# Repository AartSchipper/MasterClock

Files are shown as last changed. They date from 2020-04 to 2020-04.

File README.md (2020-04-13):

MasterClock
===========

Arduino based master clock for slave clocks. 
--------------------------------------------

* Minute or second impulses. 
* DCF-77 as a time reference. 
* Siderial, lockal or UTC time. 

This is an Arduino project that runs up to two (sets of-) slave clocks showing different types of time. It was created for the 24h second impulse clocks of the Old Leiden Observatory. 

The project consists of specially created hardware, akin to an Arduino Uno with an xtal and some interfaces, and an Arduino based firmware. The firmware is based on the DCF library and examples by: https://github.com/udoklein/dcf77, Copyright 2016 Udo Klein, GPL

Aart, 04-2020

Hardware layout
---------------

The hardware consists of an low-current 24V H-bridge per clock, the processor, a DCF receiver, a power supply and some auxilary circuits. 

A red/green duo led shows the DCF pulses and if the clock is currently synced to dcf. An extra provision is made to power and switch the lamps (24V / 12W) in the clock dials. Care was taken to use only lineair regulators and just one lighly loaded electrolitic capacitor for longelivity. The regulators are mounted on the aluminium base for cooling. 

The firmware should run on almost any Arduino compatible hardware _with a crystal_. A resonator might cause problems with the DCF library, see: https://github.com/udoklein/dcf77 

There is a standard six pin UART interface both for programming using the bootloader, and setting using a terminal. There is a jumper to disable the reset of the uC, to avoid nuisance resets in normal use. 

A known omission in the current hardware is a pull-down resistor on the gate of the MOSFET for the lights. 

The design was made in KiCad. Gerbers and a PDF of the circuits are provided.  

Firmware layout
---------------

The Dial class contains all functions related to a dial. 
dail1 & dail2 are instances of this class. 

Every millisecond sample_input_pin() is called by the DCF library.   
In this routine also Dial::DialSR(), the dial Service Routine is called to see if a puls needs to be started or stopped.   

The rest of the program runs in the main loop and is not time critical. In this loop: 
* powerCheck() stops the dails in case of power loss and stores the positions in EEPROM, so the clocks can continue automatically when power returns. 
* Check_serial_input() Handles the terminal for debugging and synchonizing the dials. 
* Dial::DoCorrection() Handles synchronising the dials to DCF, or running the dial at the correct rate in case the DCF signal is lost. 

Terminal
--------

The firmware has a simple provision for reading the time and setting the current position of the hands on the dials using the terminal:

---

Klok impuls gever 2.40 WLS, Aart 2020
> Status: 

> 109 times restarted

>Longitude: 4.46

> UTC time:       synced: Monday    2020-04-13 10:51:17 
> Local siderial: 0:37;26 
> Local time:     synced: Monday    2020-04-13 12:51:17 UTC+02

> Dial 1: Type: 24h, seconds, siderial. Position: 0:37;26 correction: 0 ms/impuls

> To set dial 1: 1hhmmss, dial 2: 2hhmmss

---

Dial type, time type and Longitude are all compile time settings. If the dial positions are not set 0:00;00 is assumed at first startup. 

Typical behaviour
-----------------

Assuming the dail positions were correct during shutdown: 
* After startup the dials run in the default speed of the time type until the DCF library is synced.  
* When the library is synced the led turns green and the hands are moved to the correct position (minute impulse dials) or stopped (second impulse dials) to wait until the correct time to start. 

Small deviations up to six minutes are corrected by making the pauses between impulses slightly longer or shorter.

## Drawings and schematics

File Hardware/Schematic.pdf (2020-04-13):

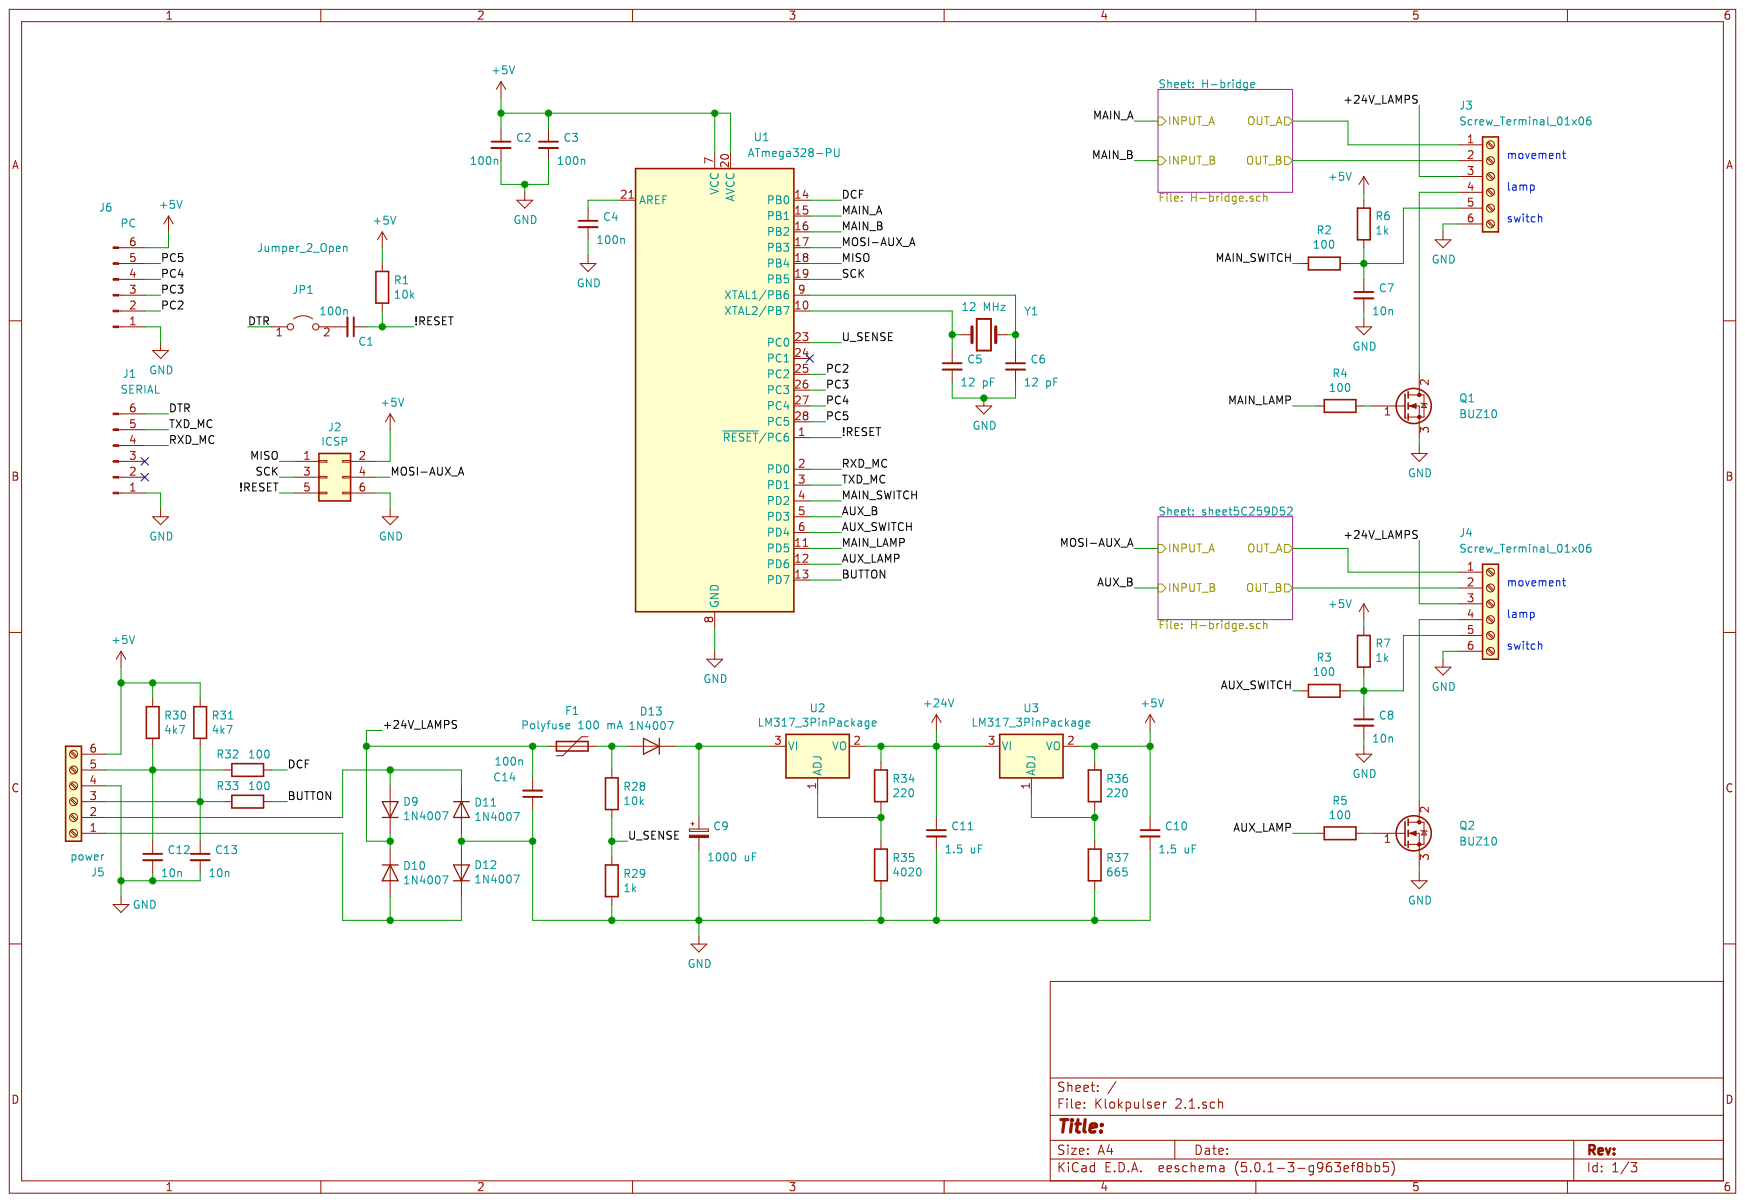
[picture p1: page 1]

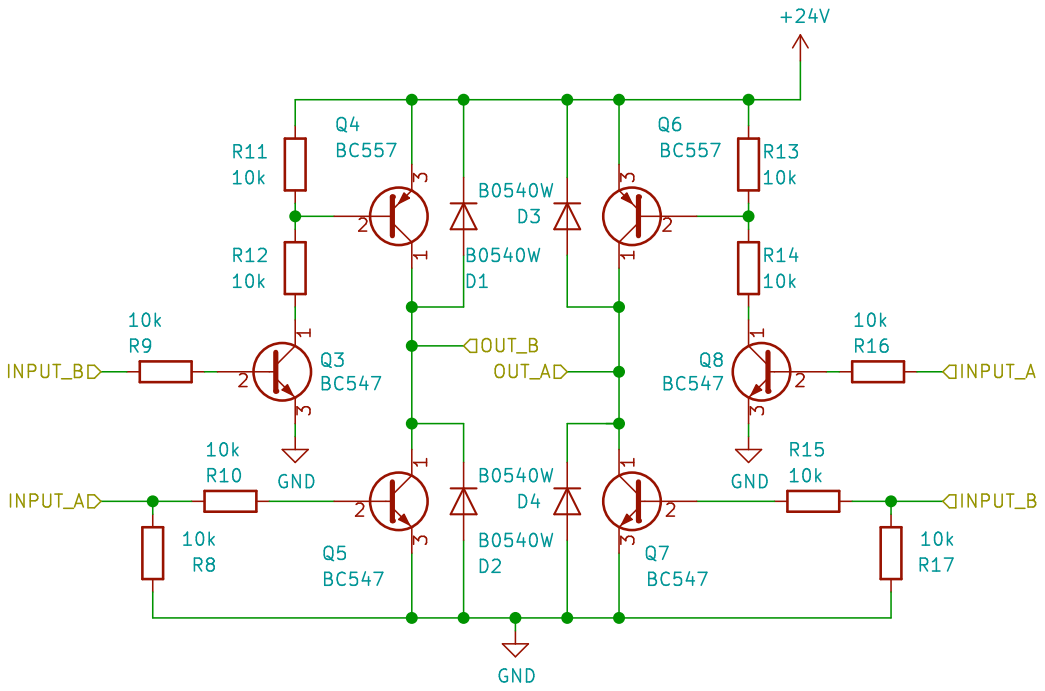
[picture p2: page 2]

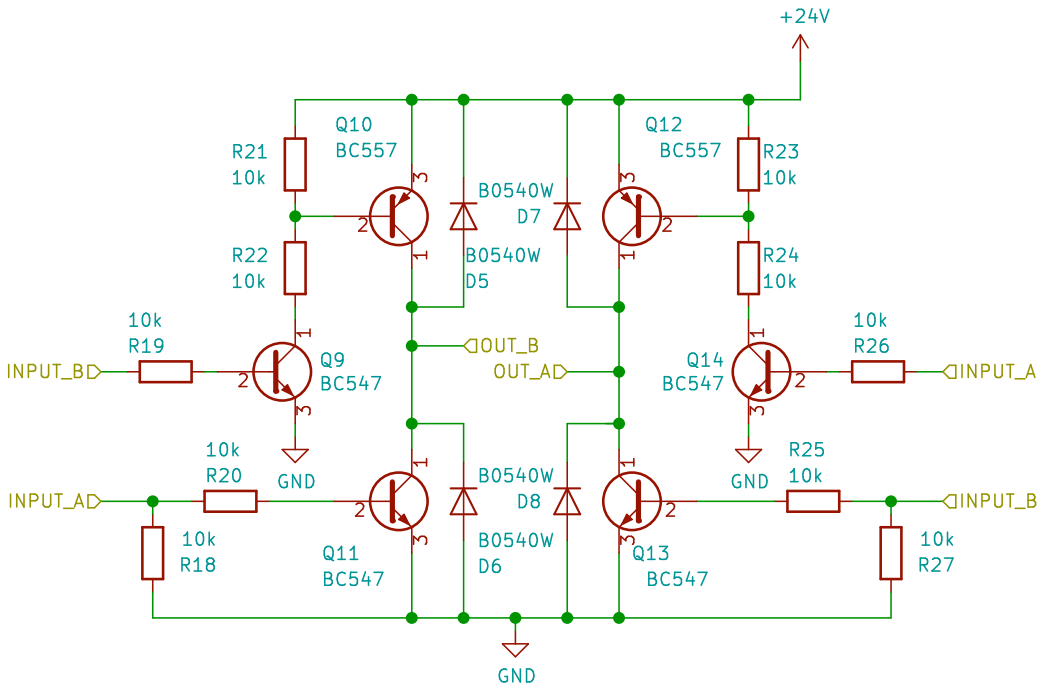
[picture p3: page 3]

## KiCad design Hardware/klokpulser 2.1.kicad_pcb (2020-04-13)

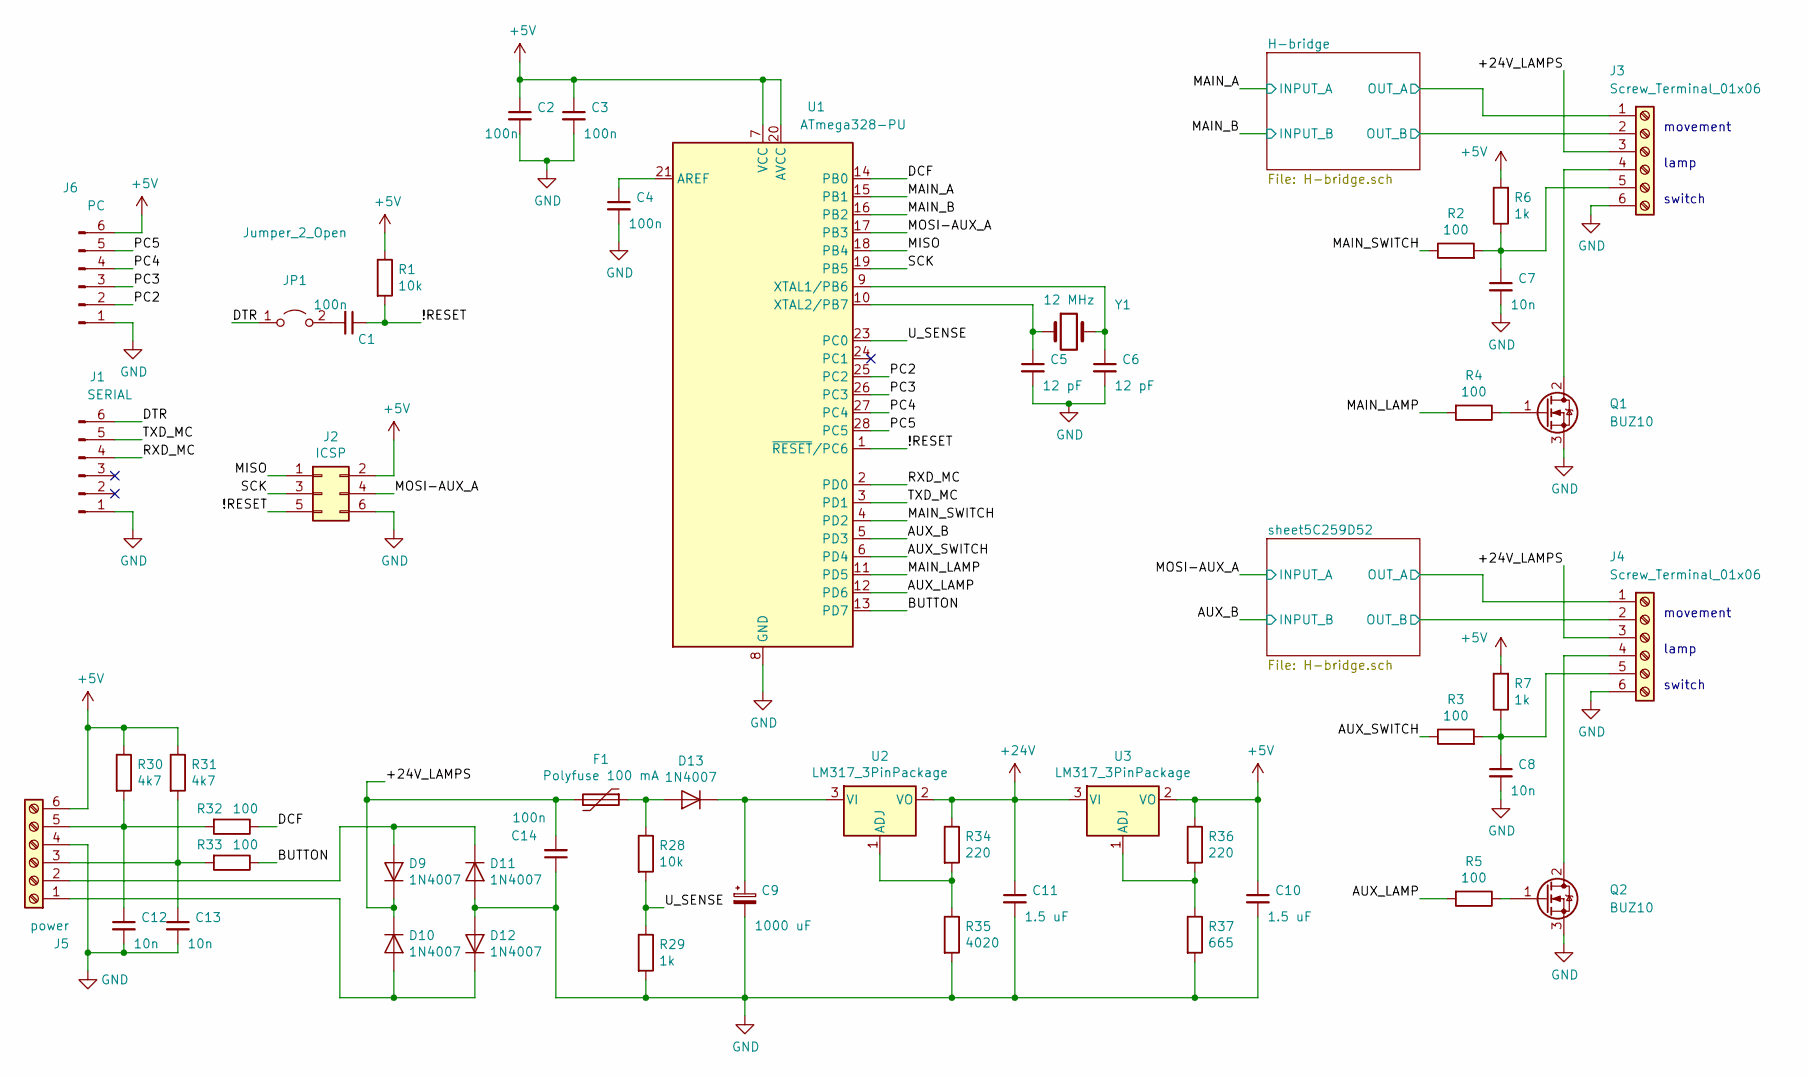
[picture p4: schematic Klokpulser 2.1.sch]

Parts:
C1, C2, C3, C4, C14: 100n; C_Rect_L7.0mm_W3.5mm_P2.50mm_P5.00mm
C5, C6: 12 pF; C_Rect_L7.0mm_W2.0mm_P5.00mm
C7, C8, C12, C13: 10n; C_Rect_L7.0mm_W3.5mm_P2.50mm_P5.00mm
C9: 1000 uF; CP_Radial_D16.0mm_P7.50mm
C10, C11: 1.5 uF; C_Rect_L7.0mm_W6.0mm_P5.00mm
D9, D10, D11, D12, D13: 1N4007; D_DO-41_SOD81_P10.16mm_Horizontal
F1: Polyfuse 100 mA; RV_Disc_D7mm_W3.4mm_P5mm
J1: SERIAL; PinHeader_1x06_P2.54mm_Vertical
J2: ICSP; PinHeader_2x03_P2.54mm_Vertical
J3, J4: Screw_Terminal_01x06; PhoenixContact_MC_1,5_6-G-3.81_1x06_P3.81mm_Horizontal
J5: power; PhoenixContact_MC_1,5_6-G-3.81_1x06_P3.81mm_Horizontal
J6: PC; PinHeader_1x06_P2.54mm_Vertical
JP1: Jumper_2_Open; PinSocket_1x02_P2.54mm_Vertical
Q1, Q2: BUZ10; TO-220-3_Vertical
R1, R28: 10k; R_Axial_DIN0207_L6.3mm_D2.5mm_P10.16mm_Horizontal
R2, R3, R4, R5, R32, R33: 100; R_Axial_DIN0207_L6.3mm_D2.5mm_P10.16mm_Horizontal
R6, R7, R29: 1k; R_Axial_DIN0207_L6.3mm_D2.5mm_P10.16mm_Horizontal
R30, R31: 4k7; R_Axial_DIN0207_L6.3mm_D2.5mm_P10.16mm_Horizontal
R34, R36: 220; R_Axial_DIN0207_L6.3mm_D2.5mm_P10.16mm_Horizontal
R35: 4020; R_Axial_DIN0207_L6.3mm_D2.5mm_P10.16mm_Horizontal
R37: 665; R_Axial_DIN0207_L6.3mm_D2.5mm_P10.16mm_Horizontal
U1: ATmega328-PU; DIP-28_W7.62mm
U2, U3: LM317_3PinPackage; TO-220-3_Horizontal_TabDown
Y1: 12 MHz; Crystal_HC49-U_Vertical

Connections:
+5V: C2.1, C3.1, C10.1, J2.2, J5.6, J6.6, R1.1, R6.2, R7.2, R30.1, R31.1, R36.1, U1.7 (VCC), U1.20 (AVCC), U3.2 (VO)
+24V: C11.1, R34.1, U2.2 (VO), U3.3 (VI); also elsewhere on the board
/!RESET: C1.1, J2.5, R1.2, U1.1 (~RESET~/PC6)
/+24V_LAMPS: C14.2, D9.1 (K), D10.1 (K), F1.2, J3.3, J4.3
/AUX_B: U1.5 (PD3); also elsewhere on the board
/AUX_LAMP: R5.2, U1.12 (PD6)
/AUX_SWITCH: R3.1, U1.6 (PD4)
/BUTTON: R33.1, U1.13 (PD7)
/DCF: R32.1, U1.14 (PB0)
/DTR: J1.6, JP1.1 (A)
/H-bridge/OUT_A: J3.1; also elsewhere on the board
/H-bridge/OUT_B: J3.2; also elsewhere on the board
/MAIN_A: U1.15 (PB1); also elsewhere on the board
/MAIN_B: U1.16 (PB2); also elsewhere on the board
/MAIN_LAMP: R4.2, U1.11 (PD5)
/MAIN_SWITCH: R2.1, U1.4 (PD2)
/MISO: J2.1, U1.18 (PB4)
/MOSI-AUX_A: J2.4, U1.17 (PB3); also elsewhere on the board
/PC2: J6.2, U1.25 (PC2)
/PC3: J6.3, U1.26 (PC3)
/PC4: J6.4, U1.27 (PC4)
/PC5: J6.5, U1.28 (PC5)
/RXD_MC: J1.4, U1.2 (PD0)
/SCK: J2.3, U1.19 (PB5)
/TXD_MC: J1.5, U1.3 (PD1)
/U_SENSE: R28.2, R29.1, U1.23 (PC0)
/sheet5C259D52/OUT_A: J4.1; also elsewhere on the board
/sheet5C259D52/OUT_B: J4.2; also elsewhere on the board
GND: C2.2, C3.2, C4.2, C5.2, C6.2, C7.2, C8.2, C9.2, C10.2, C11.2, C12.2, C13.2, C14.1, D11.2 (A), D12.2 (A), J1.1, J2.6, J3.6, J4.6, J5.4, J6.1, Q1.3 (S), Q2.3 (S), R29.2, R35.2, R37.2, U1.8 (GND), U1.22 (GND); also elsewhere on the board
unnamed: C1.2, JP1.2 (B)
unnamed: C4.1, U1.21 (AREF)
unnamed: C5.1, U1.10 (XTAL2/PB7), Y1.1
unnamed: C6.1, U1.9 (XTAL1/PB6), Y1.2
unnamed: C7.1, J3.5, R2.2, R6.1
unnamed: C8.1, J4.5, R3.2, R7.1
unnamed: C9.1, D13.1 (K), U2.3 (VI)
unnamed: C12.1, J5.5, R30.2, R32.2
unnamed: C13.1, J5.3, R31.2, R33.2
unnamed: D10.2 (A), D12.1 (K), J5.1
unnamed: D9.2 (A), D11.1 (K), J5.2
unnamed: D13.2 (A), F1.1, R28.1
unnamed: J3.4, Q1.2 (D)
unnamed: J4.4, Q2.2 (D)
unnamed: Q1.1 (G), R4.1
unnamed: Q2.1 (G), R5.1
unnamed: R34.2, R35.1, U2.1 (ADJ)
unnamed: R36.2, R37.1, U3.1 (ADJ)

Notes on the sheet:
movement
lamp
switch

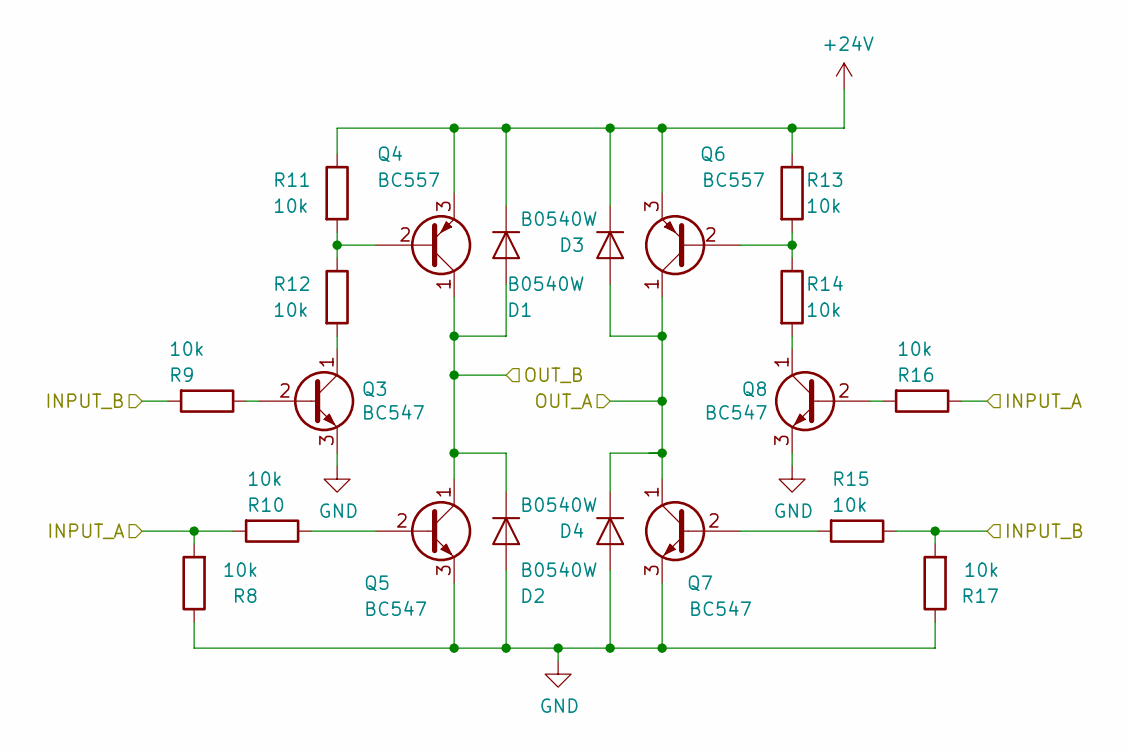
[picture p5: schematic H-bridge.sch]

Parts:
D1, D2, D3, D4: B0540W; D_DO-41_SOD81_P10.16mm_Horizontal
Q3, Q5, Q7, Q8: BC547; TO-92_Inline
Q4, Q6: BC557; TO-92_Inline
R8, R9, R10, R11, R12, R13, R14, R15, R16, R17: 10k; R_Axial_DIN0207_L6.3mm_D2.5mm_P10.16mm_Horizontal

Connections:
+24V: D1.1 (K), D3.1 (K), Q4.3 (E), Q6.3 (E), R11.1, R13.1; also elsewhere on the board
/H-bridge/OUT_A: D3.2 (A), D4.1 (K), Q6.1 (C), Q7.1 (C); also elsewhere on the board
/H-bridge/OUT_B: D1.2 (A), D2.1 (K), Q4.1 (C), Q5.1 (C); also elsewhere on the board
/MAIN_A: R8.2, R10.2, R16.1; also elsewhere on the board
/MAIN_B: R9.2, R15.1, R17.2; also elsewhere on the board
GND: D2.2 (A), D4.2 (A), Q3.3 (E), Q5.3 (E), Q7.3 (E), Q8.3 (E), R8.1, R17.1; also elsewhere on the board
unnamed: Q3.1 (C), R12.2
unnamed: Q3.2 (B), R9.1
unnamed: Q4.2 (B), R11.2, R12.1
unnamed: Q5.2 (B), R10.1
unnamed: Q6.2 (B), R13.2, R14.1
unnamed: Q7.2 (B), R15.2
unnamed: Q8.1 (C), R14.2
unnamed: Q8.2 (B), R16.2

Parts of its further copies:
D5, D6, D7, D8: B0540W; D_DO-41_SOD81_P10.16mm_Horizontal
Q9, Q11, Q13, Q14: BC547; TO-92_Inline
Q10, Q12: BC557; TO-92_Inline
R18, R19, R20, R21, R22, R23, R24, R25, R26, R27: 10k; R_Axial_DIN0207_L6.3mm_D2.5mm_P10.16mm_Horizontal

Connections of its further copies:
+24V: D5.1 (K), D7.1 (K), Q10.3 (E), Q12.3 (E), R21.1, R23.1; also elsewhere on the board
/AUX_B: R19.2, R25.1, R27.2; also elsewhere on the board
/MOSI-AUX_A: R18.2, R20.2, R26.1; also elsewhere on the board
/sheet5C259D52/OUT_A: D7.2 (A), D8.1 (K), Q12.1 (C), Q13.1 (C); also elsewhere on the board
/sheet5C259D52/OUT_B: D5.2 (A), D6.1 (K), Q10.1 (C), Q11.1 (C); also elsewhere on the board
GND: D6.2 (A), D8.2 (A), Q9.3 (E), Q11.3 (E), Q13.3 (E), Q14.3 (E), R18.1, R27.1; also elsewhere on the board
unnamed: Q9.1 (C), R22.2
unnamed: Q9.2 (B), R19.1
unnamed: Q10.2 (B), R21.2, R22.1
unnamed: Q11.2 (B), R20.1
unnamed: Q12.2 (B), R23.2, R24.1
unnamed: Q13.2 (B), R25.2
unnamed: Q14.1 (C), R24.2
unnamed: Q14.2 (B), R26.2

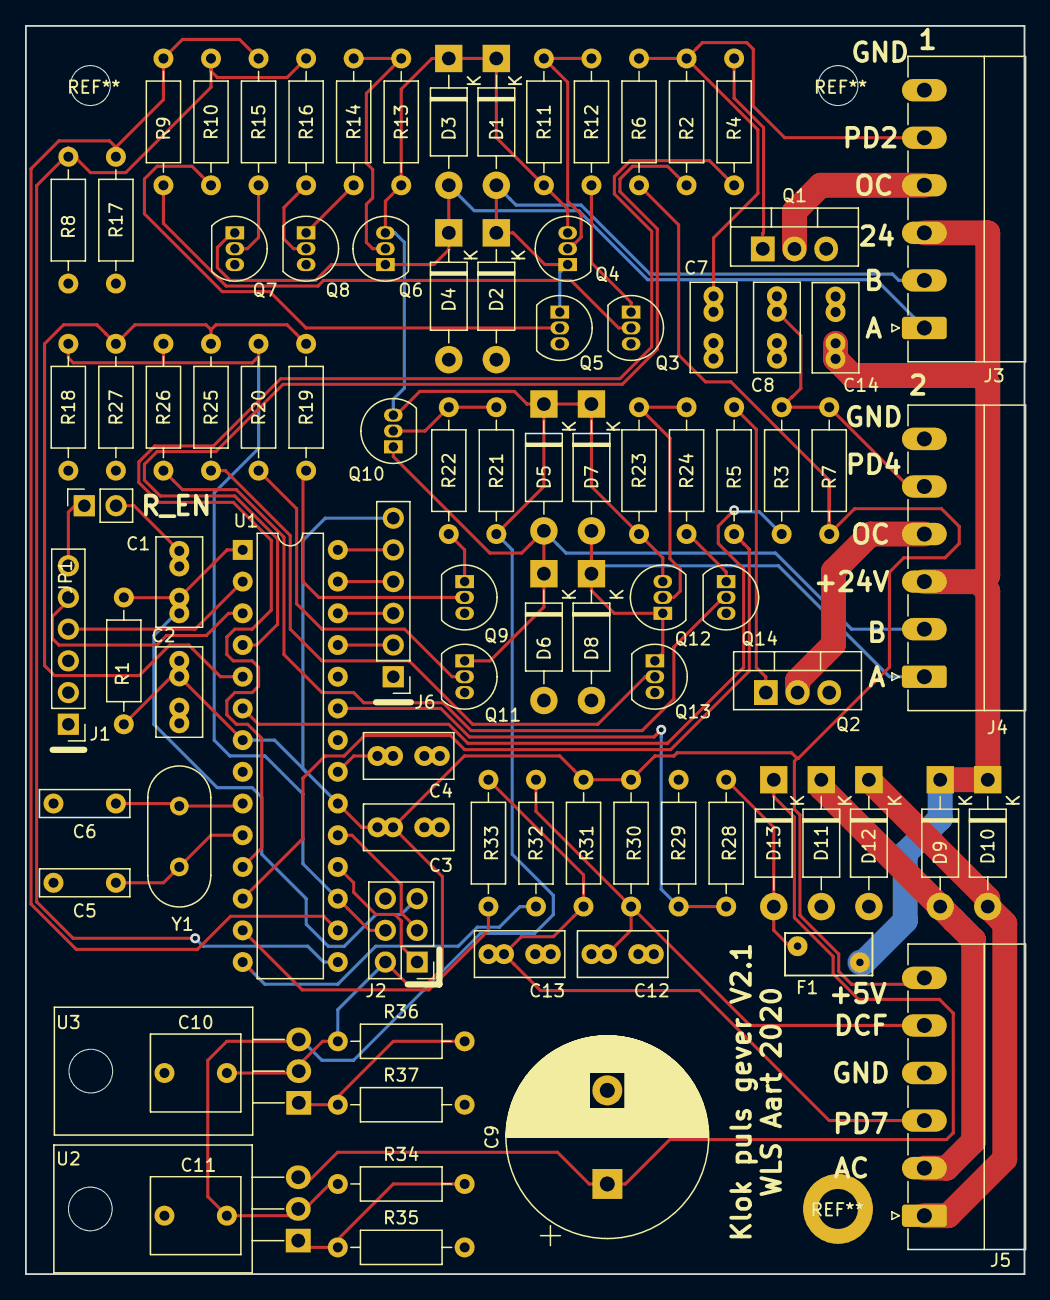
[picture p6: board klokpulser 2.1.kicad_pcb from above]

Board: 2 copper layers, 80.0 x 100.0 mm, 90 parts (0 on the bottom side), 63 nets.

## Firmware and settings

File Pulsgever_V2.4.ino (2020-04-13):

/*
  Siderial clock impulse

  Aart for WLS, started 09-2019

  Based on the DCF library and example by:
  www.blinkenlight.net, Copyright 2016 Udo Klein, GPL

  Siderial time routine adapted from:
  https://langster1980.blogspot.com/2015/11/arduino-sidereal-clock-using-gps-module.html

  Serial setting: 115200 baud

  Dial object based on klokpulsgever_1.3

  Todo: - Test with minute dial
  
  
*/

// VERSION
#define VERSION 2.4                 // As reported on serial connection.   

// Debug flags. Normal function of C2 is Green led
// #define DB_PULSE_INTERRUPT       // C2 high during 1ms interrupt activity. disables normal led function. 14 us with one dial, 17 with two.
// #define DB_PULSE_DIALS           // C2 high during DoCorrection() of all dials. 12 us when running fractional, 350 us when locked to DCF
// #define DB_SERIAL_TICK           // Sends Period, Realperiod, Correction variables per tick over serial. Use only with one dial.
// #define DB_POWER                 // Sends info about the power detection

#define MILLS_TYPE uint32_t         // can be set from uint32_t to to uint16_t for overflow testing of milliseconds in 65 seconds. 

// Includes
#include <EEPROM.h>
#include <dcf77.h>
#include "Dial.h"

// Constants
// Time type
const uint8_t LOCAL     = 1;
const uint8_t SIDERIAL  = 2;
const uint8_t UTC       = 3;

// Dial type
const uint8_t SEC24    = 1;   // 24h dial seconds impulse
const uint8_t MINUTE24 = 2;   // 24h dial minute impulse
const uint8_t SEC12    = 3;   // 12h dial seconds impulse
const uint8_t MINUTE12 = 4;   // 12h dial minute impulse

// *** USER SETTINGS *** 

// #define SECONDARY_DIAL        // Comment out when using one dial or during debugging. 

// Lokal Offset to UTC.
const int8_t timezone_offset = 1;  // Leiden (Amsterdam) = +1
const uint8_t timezone_DST = 1;      // Local timezone uses daylight saving time

// Longitude for calculation of siderial time
const float LONGITUDE = 4.463; // 4.463 home, 4.483 Observatory

// Dial (PinA, PinB, Pulsems, timeType, dialType )
// Pin A and pin B are the inputs of the H-bridge for the coil of the clock.
// Pulsems is the length of the pulses in ms.

Dial dial1 (9,  10,  300,  SIDERIAL,  SEC24);

#ifdef SECONDARY_DIAL
  Dial dial2 (3,  11,  300,  LOCAL,     SEC24);
#endif

const uint16_t LAMP_AUTO_OFF = 3600; // 3600 s = 1 h

// *** END OF USER SETTINGS ****

// pins Switches and lamps 
const uint8_t LAMP1   = 5;
const uint8_t SWITCH1 = 2;
const uint8_t LAMP2   = 6;
const uint8_t SWITCH2 = 4;

// Voltage measurement / power detect settins
#define USENSE A0                   // 1:10 Voltage divider to raw DC bus 
const int U_UNDER = 500;            // adc ticks for loss of power detect. About 16V
const int U_RETURN = 600;           // adc ticks for return of power detect. About 22V
const MILLS_TYPE U_TIME = 3;        // ms between power checks 
const uint8_t U_LOSS_COUNTER = 10;      // amount of times the checked USENSE was under U_UNDER before loss of power is detected. Nessesary because a pulsating DC is measured

// DCF Hardware & monitor led. 
const uint8_t dcf77_sample_pin = 8;                 // = B5
const uint8_t dcf77_monitor_led_red = 16;           // = C2
const uint8_t dcf77_monitor_led_green = 17;         // = C3
int dcf77_monitor_led = dcf77_monitor_led_red;      // Global variable for led color to keep interrupt as short as possible

// Dependand on receiver module:
const uint8_t dcf77_inverted_samples = 0;
const uint8_t dcf77_pin_mode = INPUT_PULLUP;  // enable internal pull up

// *** END OF SETTINGS

// Global milliseconds counter
volatile MILLS_TYPE milliseconds = 0;          // Montone counter. Only counting up to avoid rollover problems.

// EEPROM addresses
const uint8_t FLAG_EEPROM = 0;
const uint8_t DIAL1EEPROM = 1;
const uint8_t DIAL2EEPROM = 10;
const uint8_t COUNTER = 30;

// Necessary declaration
namespace Timezone {
  void adjust(Clock::time_t &time, const int8_t offset);
}


// DCF hardware sampling routine. Also 1ms interrupt for counting millseconds and running dials.
uint8_t sample_input_pin() {
  
  #ifdef DB_PULSE_INTERRUPT
    digitalWrite(A2, HIGH);
  #endif
  
  const uint8_t sampled_data = dcf77_inverted_samples ^ digitalRead(dcf77_sample_pin);
  
  #ifndef DB_PULSE_DIALS
    #ifndef DB_PULSE_INTERRUPT
      digitalWrite(dcf77_monitor_led, sampled_data);
    #endif
  #endif

  milliseconds++;

  dial1.DialSR();
  #ifdef SECONDARY_DIAL
    dial2.DialSR();
  #endif
  
  #ifdef DB_PULSE_INTERRUPT
    digitalWrite(A2, LOW);
  #endif
  
  return sampled_data;
}


// EEPROM functions for storing readouts
// Source of these functions: https://playground.arduino.cc/Code/EEPROMWriteAnything/`
template <class T> int EEPROM_writeAnything(int ee, const T& value) {
  
  const byte* p = (const byte*)(const void*)&value;
  unsigned int i;
  
  for (i = 0; i < sizeof(value); i++)
    EEPROM.write(ee++, *p++);
  return i;
}

template <class T> int EEPROM_readAnything(int ee, T& value) {
  
  byte* p = (byte*)(void*)&value;
  unsigned int i;
  
  for (i = 0; i < sizeof(value); i++)
    *p++ = EEPROM.read(ee++);
  return i;
}


// Check for power loss and act
void powerCheck(void) {
  static MILLS_TYPE lastMilliseconds;
  static int uLossCounter = 0; 

  if ((milliseconds - lastMilliseconds) < U_TIME) { // once in U_TIME ms
    return; 
  }

  lastMilliseconds = milliseconds;
   
  int usense = analogRead(USENSE);
  
  if (usense < U_UNDER) {              
    uLossCounter++; 

    #ifdef DB_POWER    
      if (uLossCounter > 2) {
        Serial.print("u loss counter: "); Serial.println (uLossCounter); // debugging
        Serial.print("u sense: "); Serial.println (usense); // debugging
        Serial.print("Millis: "); Serial.println (milliseconds); // debugging 
        Serial.println(" "); 
      }  
    #endif
    
    if (uLossCounter < U_LOSS_COUNTER) { 
      return; 
    }

    Serial.println("Loss of power ! ");         
  
    dial1.WriteEEPROM(DIAL1EEPROM);
    #ifdef SECONDARY_DIAL
      dial2.WriteEEPROM(DIAL2EEPROM);
    #endif

    EEPROM.write(FLAG_EEPROM, true); // Flag data is stored
    Serial.println("Dial positions stored in EEPROM");

    dial1.RunStop(0);
    #ifdef SECONDARY_DIAL
      dial2.RunStop(0);
    #endif

    while ( usense < U_RETURN) {
      // Wait here for possible return of power or restart
      usense = analogRead(USENSE);
    }
    Serial.println("Return of power before shutdown. ");
        
    dial1.RunStop(1);
    #ifdef SECONDARY_DIAL
      dial2.RunStop(1);
    #endif
    
    EEPROM.write(FLAG_EEPROM, false); // unflag
  } else {
    uLossCounter = 0; 
    
  }
}


void control_lamps(void) { // both lamps are controlled by the button on SWITCH1
  static int lamp;
  static MILLS_TYPE lastLamp;
  
  switch (lamp) {
    case 0:
      // lamp off
      digitalWrite (LAMP1, LOW);
      digitalWrite (LAMP2, LOW);
      
      if (milliseconds - lastLamp > 1000 && digitalRead(SWITCH1) == LOW) {
        lamp = 1;
        lastLamp = milliseconds;
        Serial.println("Lamp on.");
      }
      break;

    case 1:
      // lamp on
      digitalWrite (LAMP1, HIGH);
      digitalWrite (LAMP2, HIGH);
      
      if (milliseconds - lastLamp > 1000 && digitalRead(SWITCH1) == LOW) {
        lamp = 0;
        lastLamp = milliseconds;
        Serial.println("Lamp off.");
      }

      // Auto off
      if  (milliseconds - lastLamp > 1000 * LAMP_AUTO_OFF) {   // LAMP_AUTO_OFF in s
        lamp = 0;
        Serial.println("Lamp turned off by timer.");
      }
      break;
  }
}

void setup() { // Do once
  int startUpCounter;
  
  Serial.begin(115200);
  Serial.println();

  pinMode(dcf77_monitor_led, OUTPUT);
  pinMode(dcf77_sample_pin, dcf77_pin_mode);

  pinMode(LAMP1, OUTPUT);
  pinMode(SWITCH1, INPUT_PULLUP);
  pinMode(LAMP2, OUTPUT);
  pinMode(SWITCH2, INPUT_PULLUP);

  pinMode(USENSE, INPUT);
  analogReference(DEFAULT);

  pinMode(A2, OUTPUT);
  pinMode(A3, OUTPUT);  

  if (EEPROM.read(FLAG_EEPROM) == true) {

    dial1.ReadEEPROM(DIAL1EEPROM);
    #ifdef SECONDARY_DIAL
      dial2.ReadEEPROM(DIAL2EEPROM);
    #endif

    // Start-up counter:
    EEPROM_readAnything(COUNTER, startUpCounter);
    startUpCounter++;
    EEPROM_writeAnything(COUNTER, startUpCounter);

    EEPROM.write(FLAG_EEPROM, false); // unflag

    Serial.println("Previous dial positions read.");

  } else {
    Serial.println("Dial positions unknown.");
  }

  DCF77_Clock::setup();
  DCF77_Clock::set_input_provider(sample_input_pin);

}


// main loop, run continuosly. The DCF decoding and processing library runs "invisibly" in the timer interrupt, as does the impulses
void loop() {

  // Check for power failure
  powerCheck();

  // Handle the serial command terminal
  Check_serial_input();
  
  // Control lamps
  control_lamps();

  // Correct dials pulses. This to get fractional ms in the running OR DCF sync.
  #ifdef DB_PULSE_DIALS
    digitalWrite(A2, HIGH);
  #endif
  dial1.DoCorrection();

  #ifdef SECONDARY_DIAL
    dial2.DoCorrection();
  #endif
  #ifdef DB_PULSE_DIALS
    digitalWrite(A2, LOW);
  #endif
  
}

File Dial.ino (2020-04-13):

#include "Arduino.h" 
#include "Dial.h"

Dial::Dial(uint8_t PinA, uint8_t PinB, uint16_t Pulsems, uint8_t timeType, uint8_t dialType) {
  pinMode(PinA, OUTPUT); 
  pinMode(PinB, OUTPUT); 

  // Save public variables to private variables for use in other Dial functions
  _pinA = PinA; 
  _pinB = PinB; 
  _timeType = timeType; 
  _dialType = dialType; 
  _pulsems = Pulsems; 
  
  switch (dialType) { // Set correct _periodms and _pauseDefaultms 
    case MINUTE12:   
      _totalDialPeriods = 720;   
      switch (timeType) {
        
        case LOCAL: case UTC: 
          _periodms = 60000; 
          _pauseDefaultms = 60000 - _pulsems; 
        break; 
        case SIDERIAL:
          _periodms =  59820.2695;
          _pauseDefaultms = (uint16_t)_periodms - _pulsems;
        break; 
      }
    break; 
    
    case MINUTE24:   
      _totalDialPeriods = 1440;   
      switch (timeType) {
        case LOCAL: case UTC: 
          _periodms =  60000;
          _pauseDefaultms = (uint16_t)_periodms - _pulsems; 
        break; 
        case SIDERIAL:
          _periodms =  59820.2695; 
          _pauseDefaultms = (uint16_t)_periodms - _pulsems;
        break; 
      }
    break; 
    
    case SEC12:      
      _totalDialPeriods = 43200;  
      switch (timeType) {
        case LOCAL: case UTC: 
          _periodms =  1000; 
          _pauseDefaultms = (uint16_t)_periodms - _pulsems;
        break; 
        case SIDERIAL:
          _periodms =  997.2695; 
          _pauseDefaultms = (uint16_t)_periodms - _pulsems;
        break; 
      }
    break; 
    
    case SEC24:      
      _totalDialPeriods = 86400;  
      switch (timeType) {
        case LOCAL: case UTC: 
          _periodms =  1000; 
          _pauseDefaultms = (uint16_t)_periodms - _pulsems;
        break; 
        case SIDERIAL:
          _periodms =  997.2695; 
          _pauseDefaultms = (uint16_t)_periodms - _pulsems; 
        break; 
      }
    break; 
  }
  _maxTicks = pow(2, 32) / (uint16_t)_periodms;  // avoid rollover of millisForTicks
}; 


void Dial::SetDial (char rx_bytes[]) {
   long toSet = 0; 
   toSet += (rx_bytes[1] - '0') * 36000; 
   toSet += (rx_bytes[2] - '0') * 3600; 
   toSet += (rx_bytes[3] - '0') * 600 ; 
   toSet += (rx_bytes[4] - '0') * 60; 
   toSet += (rx_bytes[5] - '0') * 10; 
   toSet += (rx_bytes[6] - '0') * 1; 
   
   switch (_totalDialPeriods) { 
     case 86400: case 43200:
      _CurrentIndication = toSet;      // set in seconden
     break; 
     case 1440: case 720: 
      _CurrentIndication = toSet / 60; // set in minuten
     break; 
   }
}


void Dial::WriteEEPROM(uint8_t address) {
  EEPROM.write(address,_state); 
  EEPROM_writeAnything(address + 1,_CurrentIndication);  
}


void Dial::ReadEEPROM(uint8_t address) {
  _state = EEPROM.read(address); 
  EEPROM_readAnything(address + 1, _CurrentIndication);  
}


void Dial::DoCorrection () {
  switch (DCF77_Clock::get_clock_state()) {
    case Clock::useless: case Clock::dirty: 
      dcf77_monitor_led = dcf77_monitor_led_red;  
      digitalWrite (dcf77_monitor_led_green,0);       // Turn off green led if this was on
      DoFractional (); 
    break;
    
    case Clock::synced:  case Clock::locked:  
      dcf77_monitor_led = dcf77_monitor_led_green; 
      digitalWrite (dcf77_monitor_led_red,0);       // Turn off red led if this was on
      DoDCF(); 
    break;     
  }
}


void Dial::DoFractional () { 
  if (_ticks <1) return; 

  if (_ticks > _maxTicks) {         // avoid rollover
    _ticks = 0; 
    _millisecondsForTicks = 0; 
    
    #ifdef DB_SERIAL_TICK
      Serial.print("ResetMaxTicks");
    #endif
    
  }
  
  if (_ticks > _oldTicks ) {
    
    #ifdef DB_SERIAL_TICK
      Serial.print ("_ticks: "); Serial.println (_ticks); 
    #endif    
    
    realPeriod = (float) _millisecondsForTicks / (float)_ticks; 
    
    if (realPeriod < (int)_periodms) {
      _ticks = 0; 
      _millisecondsForTicks = 0;  // restart if offscale. 
    }
    
    #ifdef DB_SERIAL_TICK    
      Serial.print ("Period: "); Serial.print(_periodms); Serial.print (" RealPeriod: ");Serial.println (realPeriod,4); 
    #endif
    
    if (realPeriod < _periodms) {
      _correction = 1; 
    } else {
      _correction = 0; 
    }
    
    #ifdef DB_SERIAL_TICK    
      Serial.print ("_correction: "); Serial.println (_correction); 
    #endif
    
    _oldTicks = _ticks; 

  }
}


void Dial::DoDCF() {
  int32_t realtime, offset; 
  
  Clock::time_t now;
  DCF77_Clock::read_current_time(now);
  Timezone::adjust(now, (now.uses_summertime? -2: -1)); // Subtrackt MET/MEST offset from DCF to find UTC
  
  switch (_timeType) {
    
    case UTC: 
      realtime = nowToSeconds(now); 
    break; 
    
    case LOCAL: 
      Timezone::adjust(now, timezone_offset + (timezone_DST? (now.uses_summertime? 1:0):0));
      realtime = nowToSeconds(now); 
    break; 
    
    case SIDERIAL: 
      realtime = currentSiderealSecond(now); 
    break; 
    
  }
  
  switch (_dialType) {
    
    case MINUTE12: 
      if (realtime > 43200) realtime -=43200; 
     
    case MINUTE24: 
      realtime /= 60; 
      
      offset = _CurrentIndication - realtime; 
      if (offset > _totalDialPeriods / 2)   offset -= _totalDialPeriods; 
      if (offset < _totalDialPeriods / -2)  offset += _totalDialPeriods; // Want de klok is rond.. 
      
      if (offset == 0) _correction = 0; 
      
      if (offset = -1) _correction = -1000;    // speed 1 s up when less than 1 minutes behind
      if (offset = 1 ) _correction = 1000;     // Slow down 1s when less than 1 minutes ahead
      
      if (offset < -2 && offset > -6) _correction = -10000;   // speed 10 s up when less than 6 minutes behind
      if (offset > 2 && offset < 6) _correction = 10000;      // Slow down when less than 6 minutes ahead
      if (offset > 6 || offset < -6) _correction = -59000;    // Speed up. 
      
    break;
       
    case SEC12: 
      if (realtime > 43200) realtime -= 43200; 
    
    case SEC24:
    
      offset = _CurrentIndication - realtime; 
      if (offset > _totalDialPeriods / 2)   offset -= _totalDialPeriods; 
      if (offset < _totalDialPeriods / -2)  offset += _totalDialPeriods; 

      if (offset == 0) _correction = 0; 
      if (offset < 0 && offset > -360) _correction = -100;     // speed 0,1 s up when less than 6 minutes behind
      if (offset > 0 && offset < 360) _correction = 100;        // speed 0,1 s down when less than 6 minutes ahead
      if (offset > 360 || offset < -360) _correction = 59000;   // One pulse per minute, (almost) stop and wait. 
    break; 

// debug
    
    
  }
/* 
   if (_ticks > _oldTicks ) {   // for debug
        Serial.print("_CurrentIndication: "); Serial.println(_CurrentIndication); 
        Serial.print("Realtime: "); Serial.println(realtime); 
        Serial.print("Offset: "); Serial.println(offset); 
        _oldTicks = _ticks; 
     }
  */    
}
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

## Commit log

2020-03-08 V2.4. Replace powercheck, add local DST, refactoring
    [Dial.ino, Interface_functions.ino, Pulsgever_V2.4.ino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]
2020-04-09 Fix variable type error
    [Dial.ino, Time_functions.ino]
2020-04-13 Add hardware
    [H-bridge.sch, Klokpulser 2.1.sch, klokpulser 2.1.kicad_pcb]
